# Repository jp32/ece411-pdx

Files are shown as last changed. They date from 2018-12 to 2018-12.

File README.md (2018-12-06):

# Automated Plant Watering Device

This project enables the watering of indoor house plants without being physically present. As various plants need different watering levels, a knob (actually a potentiometer) is set by the user to determine the amount of time to water the plant, which can be set between 5 to 30 seconds. A mositure sensor is used to monitor the soil, in which water is automatically dispensed when the soil is near dry.

## Prerequisites

Boards are pre-installed with the lastest firmware. To upload the test bench firmware the latest version of the Arduino IDE is recommended (free and can be downloaded [here](https://www.arduino.cc/en/Main/Software)).

## Built With
* [Arduino](https://www.arduino.cc/en/Main/Software) - Integrated development environment
* [EAGLE](https://www.autodesk.com/products/eagle/overview) - Schematic and board layout
* [LTspice](https://www.analog.com/en/design-center/design-tools-and-calculators/ltspice-simulator.html) - Circuit simulation
* [GitHub](https://github.com/) - Version control and team collaboration

## Authors

* **Justin Patterson**
* **Jonathan Lampman**
* **Jian Meng**
* **Bruno Duergon**

## License

This project is licensed under the GNU General Public License - see the [LICENSE](LICENSE) file for details

## Acknowledgements
* **Portland State University ECE Department**
* **Andrew Greenberg**
* **Eric Ruhl**

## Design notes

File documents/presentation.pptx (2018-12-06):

## Self watering plant Group 12

Bruno Duregon
Justin Patterson
Jon Lampguy
Jian Meng

## Design matrix

| | Magnetic Gripper | Self Watering Plant | Cleaning Robot | Snack Dispening Machine
Cost | 5 | 1 | 4 | 2 | 4
Feasibility | 5 | 2 | 4 | 2 | 4
Sensor/Actuator Complexity | 2 | 3 | 5 | 2 | 3
Algorithmic Complexity | 3 | 4 | 5 | 1 | 5
Programming Requirements | 5 | 1 | 4 | 1 | 4
Time Commitment | 2 | 2 | 4 | 1 | 2
| Score | 42 | 93 | 34 | 91

## Overview of problem

- Making the home garden watering process more efficient
- Necessity to water house plants without being present
- Rethinking water usage

## Solution

- Self watering plant system
  - Periodically checks moisture level
  - Turns on when moisture level out of bounds
  - Waters appropriate amount

## Block Diagram level 0

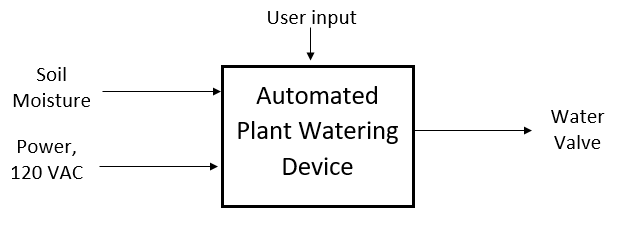
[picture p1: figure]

V DC

## Block diagram level 1

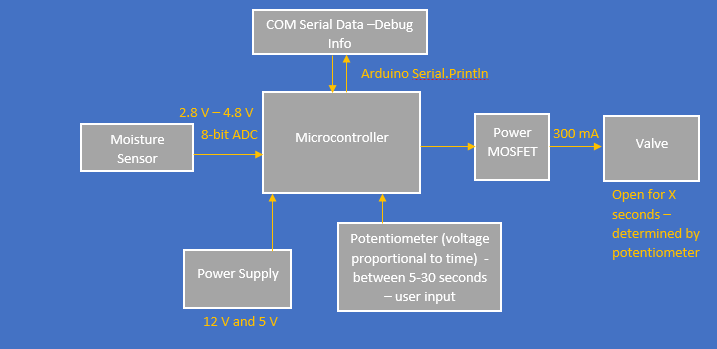
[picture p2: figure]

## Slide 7

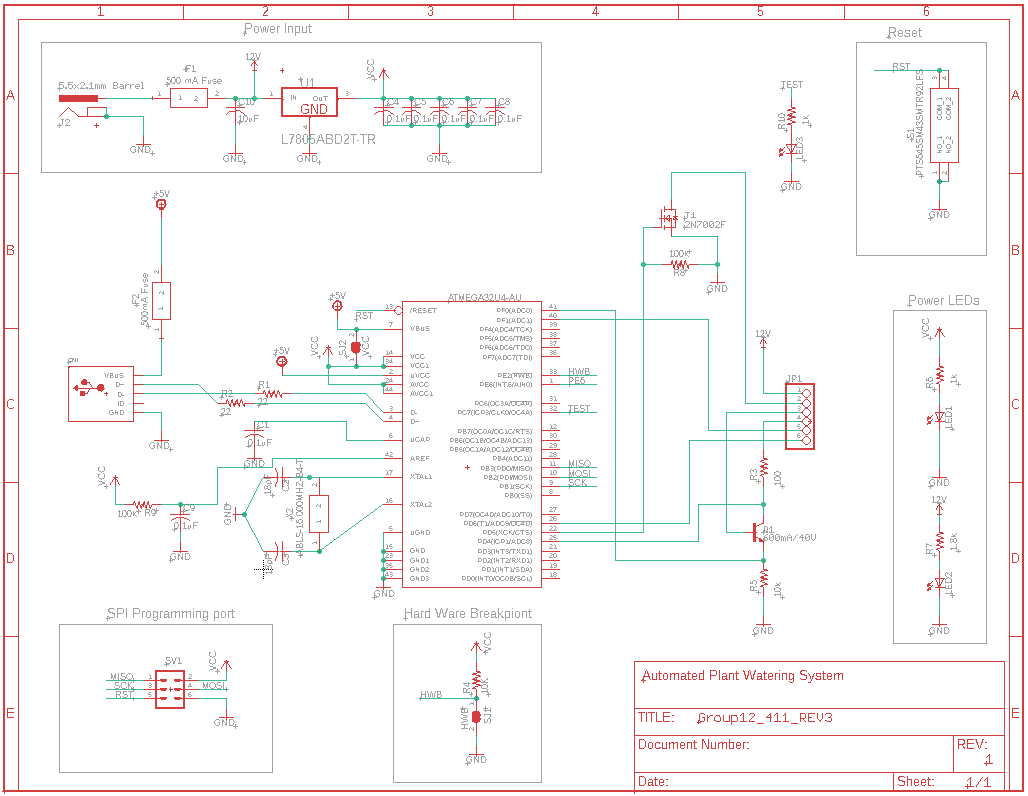
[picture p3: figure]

## layout

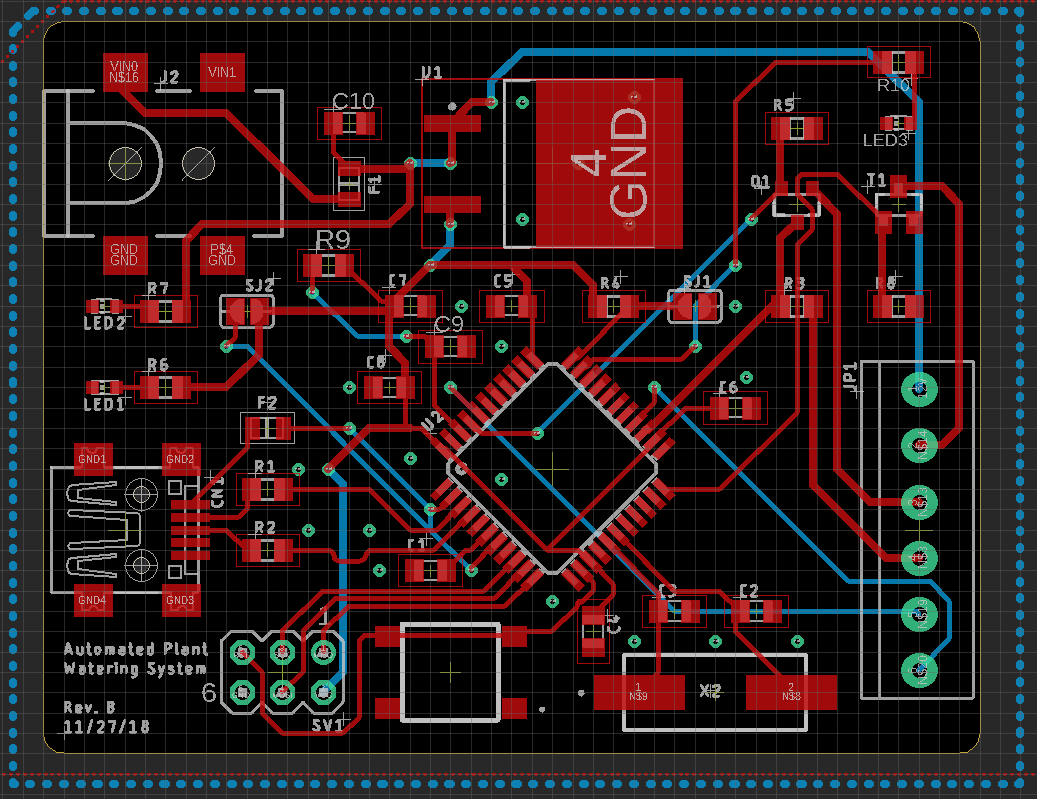
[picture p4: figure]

## Firmware overview

  - If moisture reading is lower than set bounds
    - Water plant for time specified
  - VerificTime specified by potentiometer (between 5 and 30 seconds)
  - ation of hardware via testbench
    - Valve functionalities
      - Open valve, close valve, test potentiometer
    - Sensor functionalities
      - Read sensor once, read sensor x times, read sensor and average

## Bill of Materials

Cnt | Part References | P/DNP | Mfg | Mfg PN | Description | Distributor | Dist. PN | Cost Ea. | Cost Ext.
1 | Microcontroller | P | Microchip Technology | ATMEGA32U4-AUR | AVR AVR® ATmega Microcontroller IC 8-Bit 16MHz 32KB (16K x 16) FLASH 44-TQFP (10x10) | Digikey | ATMEGA32U4-AURTR-ND | 3.49 | 3.49
1 | REG | P | STMicroelectronics | L7805ABD2T-TR | Linear Voltage Regulator IC Positive Fixed 1 Output 5V 1.5A D2PAK | Digikey | 497-1170-1-ND | 0.82 | 0.82
1 | Q1 | P | Diodes Incorporated | DMG3406L-7 | N-Channel 30V 3.6A (Ta) 770mW (Ta) Surface Mount SOT-23 | Digikey | DMG3406L-7DICT-ND | 0.53 | 0.53
2 | R1 | P | TE Connectivity Passive Product | CRGP0805F10K | 10 kOhms ±1% 0.333W, 1/3W Chip Resistor 0805 (2012 Metric) Pulse Withstanding Thick Film | Digikey | A130489TR-ND | 0.02397 | 0.04794
1 | R2 | P | TE Connectivity Passive Product | CRGP0805F100K | 100 kOhms ±1% 0.333W, 1/3W Chip Resistor 0805 (2012 Metric) Pulse Withstanding Thick Film | Digikey | A130501TR-ND | 0.02397 | 0.02397
1 | R3 | P | TE Connectivity Passive Product | CRGP0805F100R | 100 Ohms ±1% 0.333W, 1/3W Chip Resistor 0805 (2012 Metric) Pulse Withstanding Thick Film | Digikey | A130465TR-ND | 0.02397 | 0.02397
1 | R4 | P | TE Connectivity Passive Product | CRGP0805F1K0 | 1 kOhms ±1% 0.333W, 1/3W Chip Resistor 0805 (2012 Metric) Pulse Withstanding Thick Film | Digikey | A130477TR-ND | 0.02397 | 0.02397
1 | R5 | P | Vishay Dale | TNPW08051K80BEEA | 1.8 kOhms ±0.1% 0.2W, 1/5W Chip Resistor 0805 (2012 Metric) Anti-Sulfur, Automotive AEC-Q200, Moisture Resistant Thin Film | Digikey | 541-9859-1-ND | 0.63 | 0.63
2 | R6 | P | TE Connectivity Passive Product | CRGP0805F22R | 22 Ohms ±1% 0.333W, 1/3W Chip Resistor 0805 (2012 Metric) Pulse Withstanding Thick Film | Digikey | A130457TR-ND | 0.02 | 0.04
2 | C1 | P | Samsung Electro-Mechanics | CL21A106KOCLRNC | 10µF ±10% 16V Ceramic Capacitor X5R 0805 (2012 Metric) | Digikey | 1276-2399-2-ND | 0.04428 | 0.08856
6 | C2 | P | Yageo | CC0805ZRY5V9BB104 | 0.1µF -20%, +80% 50V Ceramic Capacitor Y5V (F) 0805 (2012 Metric) | Digikey | 311-1361-1-ND | 0.16 | 0.96
2 | C3 | P | KEMET | C0805C220K5GACTU | 22pF ±10% 50V Ceramic Capacitor C0G, NP0 0805 (2012 Metric) | Digikey | 399-8036-1-ND | 0.14 | 0.28
1 | X1 | P | Abracon LLC | ABLS-16.000MHZ-B4-T | 16MHz ±30ppm Crystal 18pF 40 Ohms HC-49/US | Digikey | 535-10226-1-ND | 0.27 | 0.27
2 | JMP | DNP | Vishay Dale | CRCW08050000Z0EA | 0 Ohms Jumper 0.125W, 1/8W Chip Resistor 0805 (2012 Metric) Automotive AEC-Q200 Thick Film | Digikey | 541-0.0ACT-ND | 0.1 | 0.2
1 | LED(Red) | DNP | Lite-On Inc. | LTST-C191KRKT | Red 631nm LED Indication - Discrete 2V 0603 (1608 Metric) | Digikey | 160-1447-1-ND | 0.29 | 0.29
1 | LED(Green) | DNP | Lite-On Inc. | LTST-C190GKT | Green 569nm LED Indication - Discrete 2.1V 0603 (1608 Metric) | Digikey | 160-1183-6-ND | 0.27 | 0.27
1 | I/O | P | Phoenix Contact | 1985234 | TERM BLOCK PCB 6POS 3.5MM GREEN | Digikey | 277-1626-ND | 0.85 | 0.85
1 | Q2 | P | Micro Commercial Co | MMBT3904-TP | Bipolar (BJT) Transistor NPN 40V 200mA 300MHz 350mW Surface Mount SOT-23 | Digikey | MMBT3904TPMSCT-ND | 0.1 | 0.1
1 | SW1 | P | C&K | PTS645SM43SMTR92 LFS | SWITCH TACTILE SPST-NO 0.05A 12V | Digikey | CKN9112CT-ND | 0.17 | 0.17
2 | FUSE | P | Vishay Beyschlag | MFU0805FF00500P100 | FUSE BOARD MNT 500MA 32VDC 0805 | Digikey | MFU0805.50CT-ND | 0.57 | 1.14
| | | | | | | | | 0
| | | | | | | TOTAL COST: | | $ 10.25

## Test plan 1

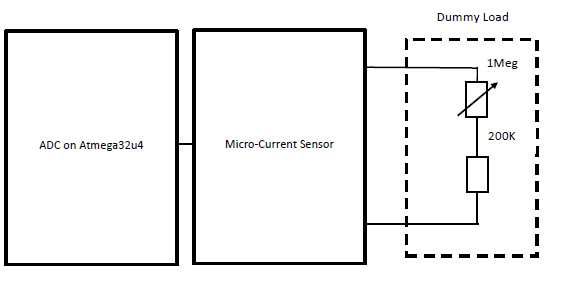
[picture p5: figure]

## Test plan 2

PART 1: Initial Power Setup
1. Before Power is provided to the board for the first time a visual inspection should be
performed by a at least one person whom is not the assembler.
2. Power module test:
a. Power cable connection test
b. Voltage regulator test
3. Power up test:
a. Current level test
b. Voltage level check
c. Leakage check: Check movement of current between two conductors that are not
connected.
d. Opens Test: Check to make sure there is current flow from one "node" to the next
for every net on the board, again by measuring the amount of resistance of the
conductor.
e. Shorts Test: Check to make sure that NO current flows between separate nets by
measuring the amount resistance between them.
2
PART 2: System test
The test session of the system includes two parts:
1. Single component test:
a. Check the type and the specification model of the sensor and actuator
b. Test the functionality of the sensor and actuator
2. System test:
a. Design Validation: PCB Layout validation and code verification.
b. Manufacturing test: Detect the manufacturing defects.
c. Function test: Follow the block diagram of the system to make sure each part of
the system can work correctly.
PART 2 - 1 - 1: Moisture sensor test (FINISHED)
A. Structure of the sensor: Moisture sensor is testing the resistance across two probes, the
moisture level of the soil is represented as the voltage value.
B. Test Method: Plug the probes into the different soil samples(each soil sample got
different level moisture), measure the returned voltage level.
C. Results: By increasing the moisture level of the sample soil, the measured maximum
voltage level is about 4.3V(Under 5V power supply voltage). The minimum voltage level
is about 2V.
PART 2 - 1 -

PART 2 - 1 - 2: Actuator Test (FINISHED)
The actuator of the automated watering system is a water valve. The I/O pin of the processor
control the ON and OFF of the actuator. When the moisture level lower than the threshold value,
3
the system will turn on the valve. In other words, the goal of the test is to make sure that the
actuator is capable for multiple ON/OFF in a short time period.
A. Test Method: Connect the valve to the output pin of the circuit, run the “Blink” file on
the circuit.
B. Results: Run the program for 2 minutes, the system will keep turning ON/OFF of the
valve, the valve worked correctly.
PART 2 - 2 - 1: PCB Validation
A. Parts completion check:
a. All major components included?
i. Processor
ii. Power supply (Voltage regulator)
iii. Moisture sensor
iv. The actuator (Valve)
b. All support components included?
i. USB connection port
ii. Power connection port
iii. Reset switch
c. All the surface mount circuit component included?
B. PCB footprint check
C. Parts placement test
PART 2 - 2 - 2: Function Test
A. Debug the code to make sure the code can successfully flash into the processor.
4
B. After the program is flashed to the processor via USB, a test run should be performed.
PART 2 - 2 - 3: Manufacturing Test
A. Follow the schematic and assemble the circuit on each board.
B. Follow the test method in PART 2 - 2 - 2 to test all the prototypes.

## what’s left to do

- Second revision of board (fix board issue)
- Put it in box – waterproof it
- More I/O for sensors and plants
- Keep historical data for seasonal average
- Add wireless communication for viewable diagnostics and statistics (phone, computer, app)

## Finalized gantt chart

## Lessons learned

- Board layout took longer than expected
- Be careful with discount power supplies
- No lull time – always stay on top of something
- Be careful soldering, we only have four boards
- Can have greater spacing between traces (it’s okay)

Jon lowkey farts a lot in the lab

## IP used

- Eagle
- LT Spice
- Microsoft Office
- GitHub (https://github.com/jp32/ece411-pdx)
- Arduino

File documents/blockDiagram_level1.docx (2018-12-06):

# Automated Plant Watering Device: Level 1

Potentiometer (voltage proportional to time) - between 5-30 seconds – user input

12 V and 5 V

Power Supply

2.8 V – 4.8 V

Arduino Serial.Println

COM Serial Data –Debug Info

300 mA

8-bit ADC

Moisture Sensor

Open for X seconds – determined by potentiometer

Valve

Power MOSFET

Microcontroller

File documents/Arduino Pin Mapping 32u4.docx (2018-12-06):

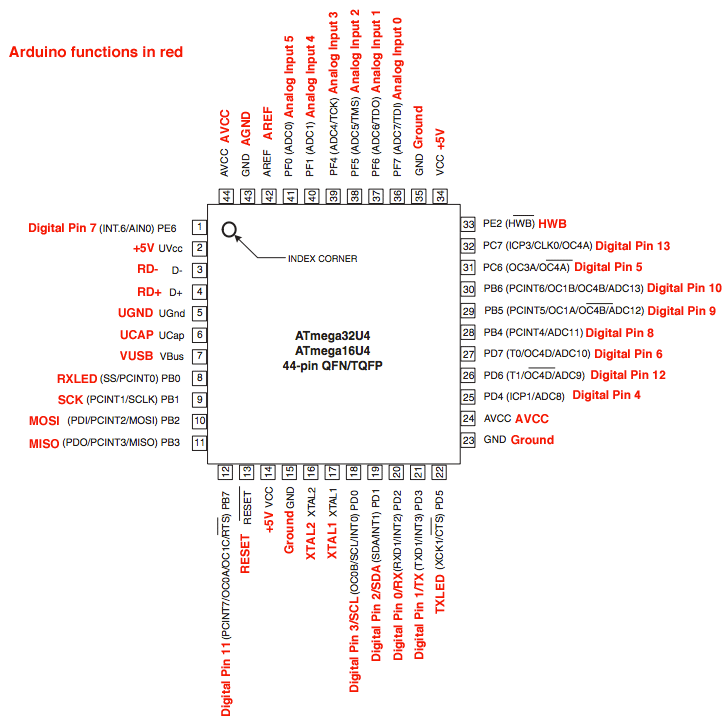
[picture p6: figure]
Image result for 32u4 arduino

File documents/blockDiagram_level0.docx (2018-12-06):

# Automated Plant Watering Device: Level 0

User input

Soil

Moisture

Automated Plant Watering Device

Water

Valve

Power,

120 VAC

Module | Automated Plant Watering Device
Inputs | Soil moisture: ?-?V Power: 120V AC rms, 60 Hz
Outputs | Water valve: voltage controlled, 12V
Functionality | Provide water to plant. The length of time the valve is open is inversely proportional to the soil moisture. i.e., Lower moisture → more water

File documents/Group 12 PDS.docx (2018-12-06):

Product Design Specification

Group 12

Justin Patterson, Jian Meng, Jonathan Lampman, Bruno Duregon

Executive Summary/Concept of Operations:

The intention of our project is to create a device that can monitor the moisture level in soil, to then appropriately open a valve to water a plant. For our project, the valve is an emulation of the device being hooked up to some real water source. It is targeted towards the average consumer, but can be used in many different applications: can be useful for plants that need to be watered rarely (potentially store historic data and water accordingly), used in any application where self-watering is required (can change watering amount decision criteria as needed), or is useful in accurately watering a plant the required amount (no overwatering, potential area to conserve resources in).

Brief Market Analysis:

The intended customers of our product are homeowners, renters, anybody with some sort of small to medium sized plant, potted or in the soil. Our product is looking to be sold around the $20 mark, as it can only serve one plant. In the future, a potential update to our product model would be to sell extension tubes so one unit could water multiple plants at a time.

Requirements:

- Must measure relative moisture content
- Must distribute water depending on relative moisture content
- Should retain semi-historic data and take it into account when decision making
- Must run on 9V battery
- Should interface to LCD screen for easily viewable information
- Should be portable

System Architecture:

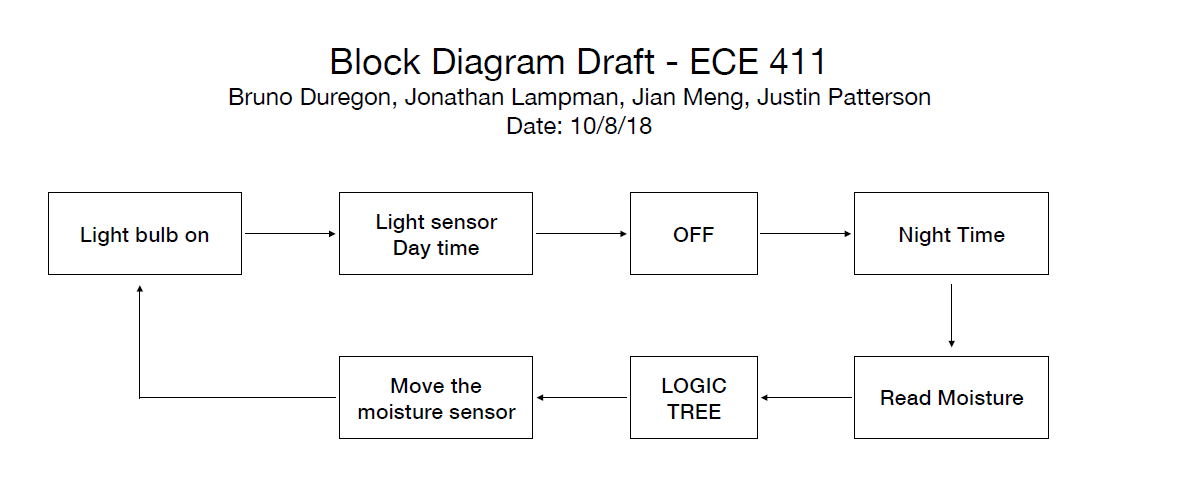
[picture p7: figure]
A screenshot of a cell phone Description generated with very high confidence

Design Specification:

- Sensor: TBD
- Actuator: Plastic Water Solenoid Valve - 12V - 1/2 Nominal, 3-116 PSI (0.21 ~ 8 bar), Connection Method: Threaded ½” NPS, 0.01 lb (4.54g)
- ATMEGA32U4 AVR 8-Bit Microcontroller, Max Clock Frequency: 16 MHz, Program Memory Size: 32 kB, Data RAM Size: 2.5 kB, ADC Resolution: 10 bit, Number of I/Os: 26 I/O, Operating Supply Voltage: 2.7 V to 5.5 V
- Arduino programmer

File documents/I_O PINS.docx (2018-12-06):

Water Valve Output: Digital Pin 1

Output High to turn on valve

Moisture Sensor Input: Analog Input 5

Most wet will be high of around 4.3 Volts

Photo Resistor out: Digital Pin 12

Photo Resistor In: Analog Input 4

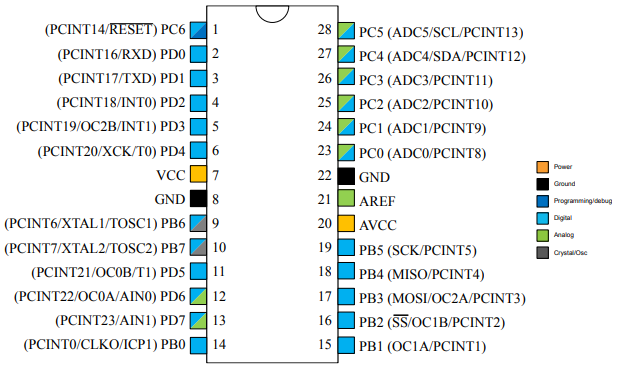
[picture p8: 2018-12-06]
datasheets/ATmega328-328P_pinout.png

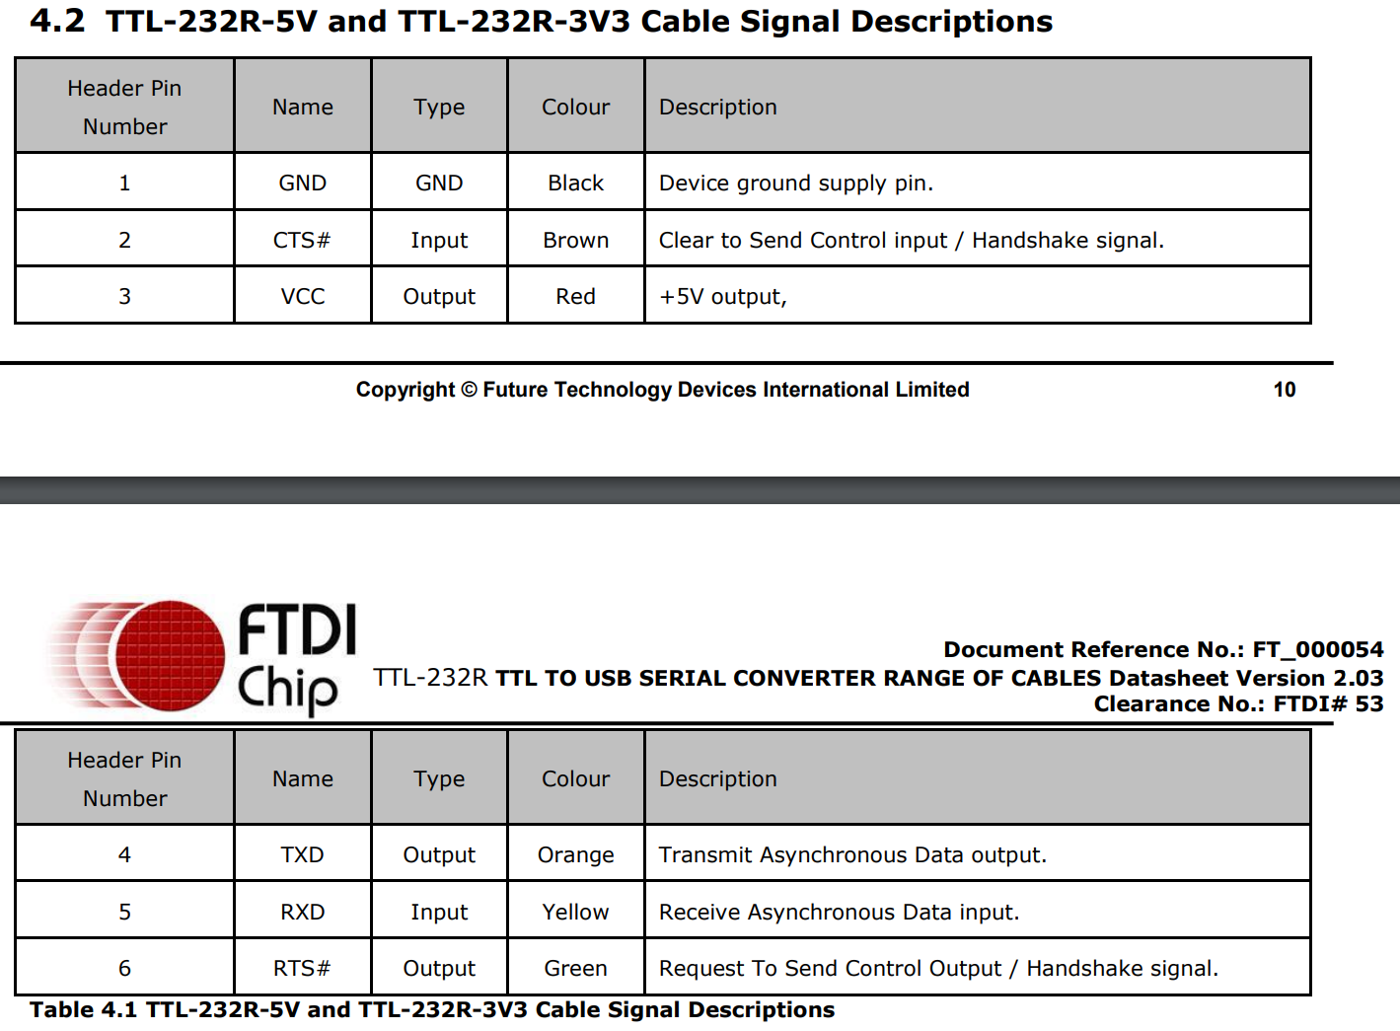
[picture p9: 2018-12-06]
datasheets/TTL-232R-5V_Cable_Signal.PNG

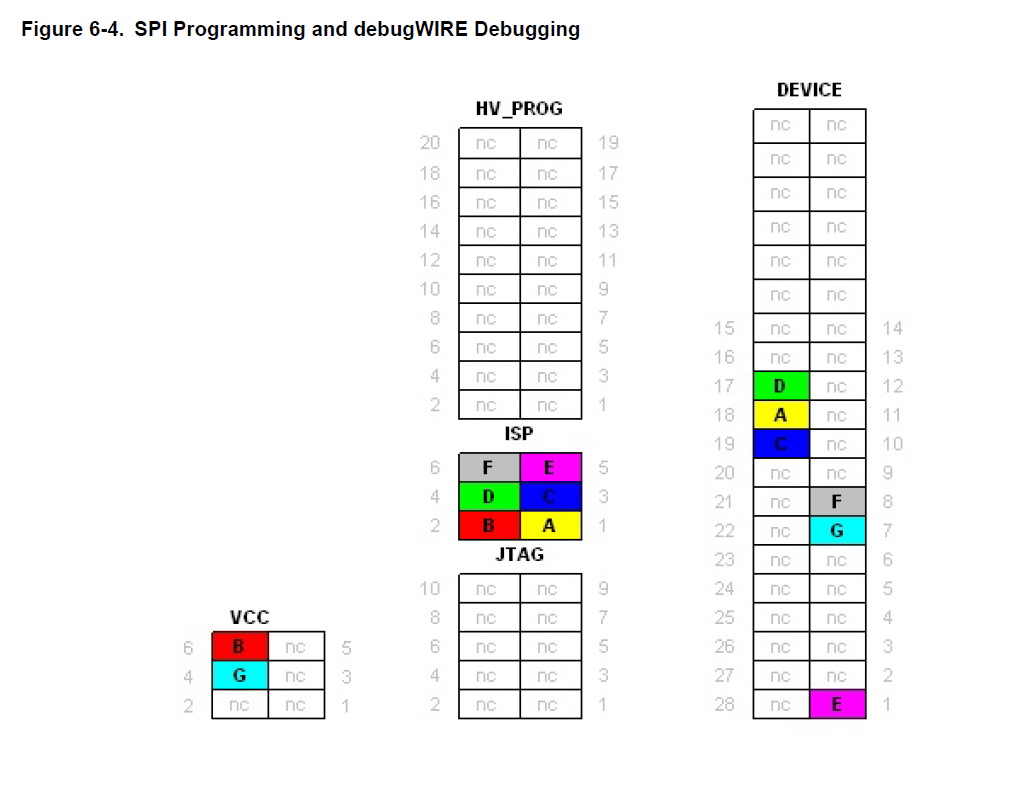
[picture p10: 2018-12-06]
datasheets/SPI_Prog.png

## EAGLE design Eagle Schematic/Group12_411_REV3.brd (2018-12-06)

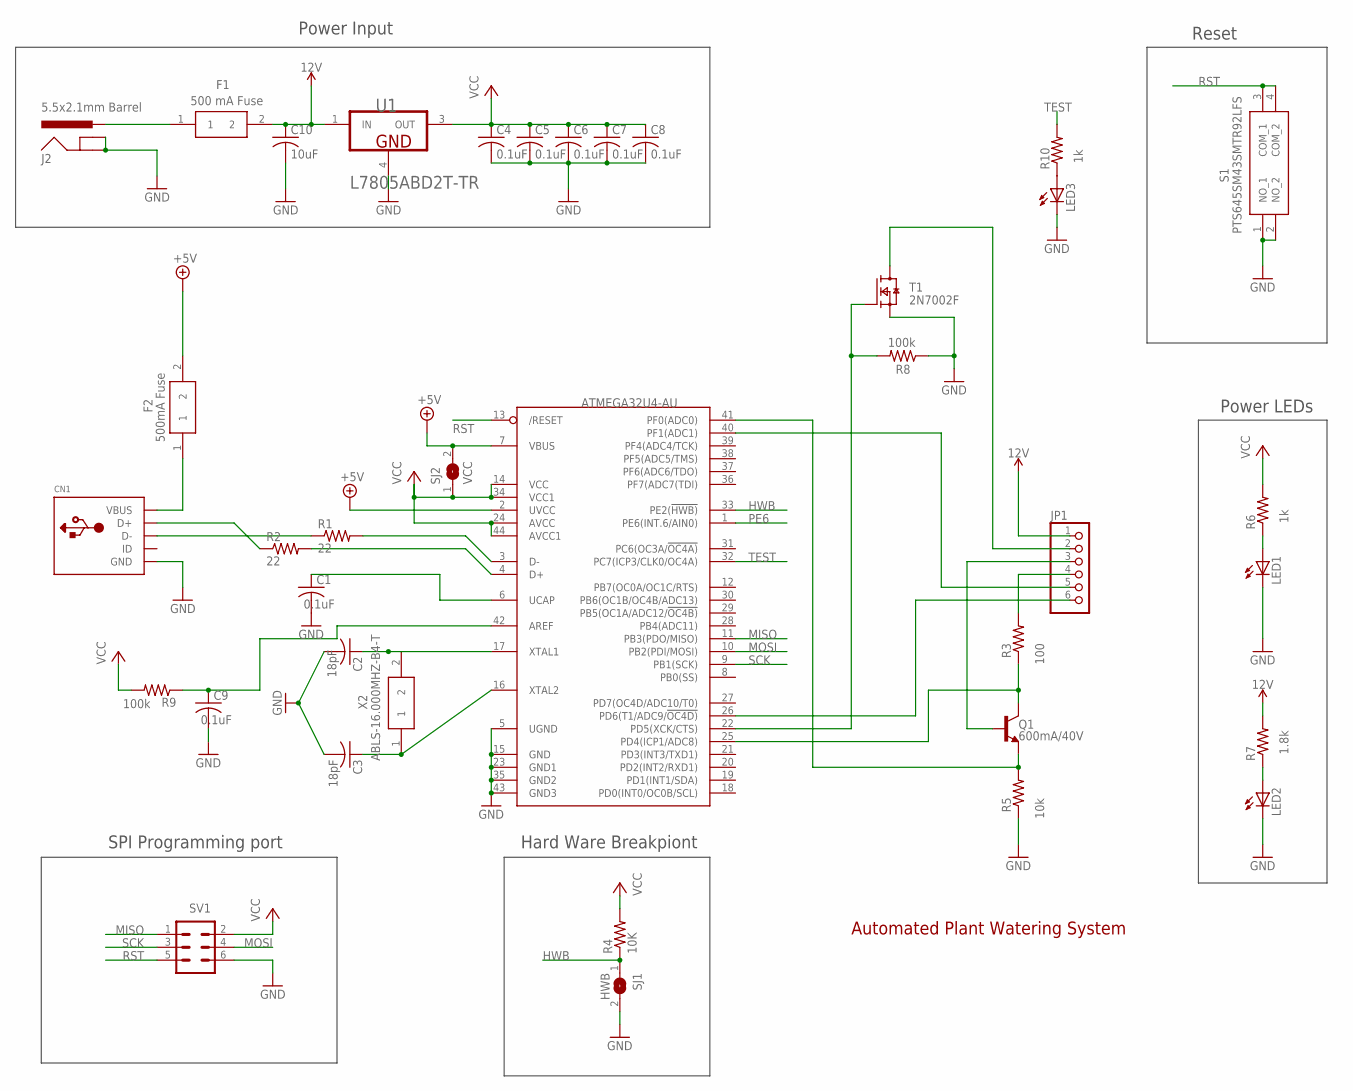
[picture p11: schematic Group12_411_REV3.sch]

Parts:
C1, C4, C5, C6, C7, C8, C9: 0.1uF; C0805K
C2, C3: 18pF; C0805K
C10: 10uF; C0805K
CN1: USBMINIB; USB-MINIB
F1: MFU0805FF00500P100; FUSC2012X55N; MANUFACTURER_PART_NUMBER 500 mA Fuse
F2: MFU0805FF00500P100; FUSC2012X55N; MANUFACTURER_PART_NUMBER 500mA Fuse
J2: 5.5x2.1mm Barrel; POWER_JACK_SMD
JP1: PINHD-1X6-3.5MM; 1X06-3.5MM
LED1, LED2, LED3: LEDCHIP-LED0603; CHIP-LED0603
Q1: 600mA/40V; SOT23-3
R1, R2, R3, R5: 22; R0805
R4, R6, R7, R8, R10: 10K; R0805
R9: 100k; R0805
S1: PTS645SM43SMTR92LFS; PTS645SMT
SJ1: HWB; SJ
SJ2: VCC; SJ
SV1: MA03-2
T1: 2N7002F; SOT23
U1: STMICROELECTRONICS_L7805ABD2T-TRSTMICROELECTRONIC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; STMICROELECTRONICS_L7805ABD2T-TR_0
U2: ATMEGA32U4-AU; TQFP44
X2: ABLS-16.000MHZ-B4-T; ABLS

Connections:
12V: C10.1, F1.2, JP1.1, R7.2, U1.1 (IN)
+5V: F2.2, SJ2.2, U2.2 (UVCC), U2.7 (VBUS)
GND: C1.2, C2.2, C3.2, C4.2, C5.2, C6.2, C7.2, C8.2, C9.2, C10.2, CN1.GND, J2.GND (GNDBREAK), J2.P$4 (GND), LED1.C, LED2.C, LED3.C, R5.1, R8.1, S1.1 (NO_1), S1.2 (NO_2), SJ1.2, SV1.6, T1.2 (S), U1.4 (GND), U2.5 (UGND), U2.15 (GND), U2.23 (GND1), U2.35 (GND2), U2.43 (GND3)
HWB: R4.1, SJ1.1, U2.33 (PE2(!HWB))
MISO: SV1.1, U2.11 (PB3(PDO/MISO))
MOSI: SV1.4, U2.10 (PB2(PDI/MOSI))
unnamed: LED3.A, R10.1
unnamed: CN1.D+, R2.1
unnamed: JP1.4, R3.2
unnamed: R2.2, U2.4 (D+)
unnamed: CN1.D-, R1.1
unnamed: C1.1, U2.6 (UCAP)
unnamed: R1.2, U2.3 (D-)
unnamed: C2.1, U2.17 (XTAL1), X2.2
unnamed: C3.1, U2.16 (XTAL2), X2.1
unnamed: LED1.A, R6.1
unnamed: Q1.3 (C), R3.1, U2.25 (PD4(ICP1/ADC8))
unnamed: Q1.2 (E), R5.2, U2.41 (PF0(ADC0))
unnamed: JP1.3, Q1.1 (B)
unnamed: JP1.2, T1.3 (D)
unnamed: LED2.A, R7.1
unnamed: F1.1, J2.VIN0 (PWR)
unnamed: CN1.VBUS, F2.1
unnamed: R8.2, T1.1 (G), U2.22 (PD5(XCK/CTS))
unnamed: JP1.5, U2.40 (PF1(ADC1))
unnamed: JP1.6, U2.26 (PD6(T1/ADC9/!OC4D))
unnamed: C9.1, R9.1, U2.42 (AREF)
PE6: U2.1 (PE6(INT.6/AIN0))
RST: S1.3 (COM_1), S1.4 (COM_2), SV1.5, U2.13 (/RESET)
SCK: SV1.3, U2.9 (PB1(SCK))
TEST: R10.2, U2.32 (PC7(ICP3/CLK0/OC4A))
VCC: C4.1, C5.1, C6.1, C7.1, C8.1, R4.2, R6.2, R9.2, SJ2.1, SV1.2, U1.3 (OUT), U2.14 (VCC), U2.24 (AVCC), U2.34 (VCC1), U2.44 (AVCC1)

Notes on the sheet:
Automated Plant Watering System
Power Input
Reset
Power LEDs
SPI Programming port
Hard Ware Breakpiont

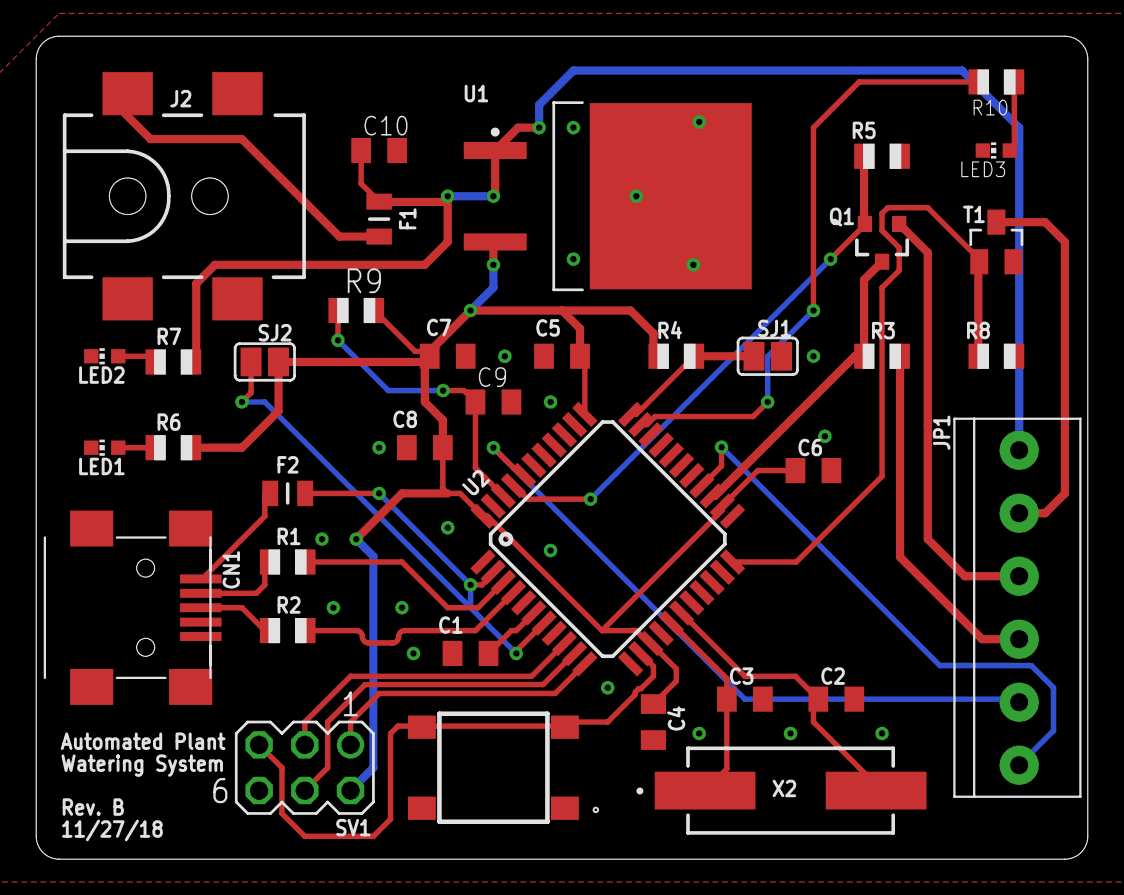
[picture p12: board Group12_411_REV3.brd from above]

Board: 2 copper layers, 58.4 x 45.7 mm, 37 parts (0 on the bottom side), 31 nets.

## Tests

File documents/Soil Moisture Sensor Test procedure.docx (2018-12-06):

Soil Moisture Sensor Test procedure

Dummy Load

ADC on Atmega32u4

Micro-Current Sensor

1Meg

200K

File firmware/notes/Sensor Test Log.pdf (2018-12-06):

Friday, November 30, 2018

## Sensor Test

Moisture sensor test

- Lower bound: 3.6V - 658 digital value - 1Mega ohms
- Upper bound: 4.7V - 896 digital value - 120 ohms
- Middle value: 4.0 V - 764 digital value - 0.436 Mega ohms

1

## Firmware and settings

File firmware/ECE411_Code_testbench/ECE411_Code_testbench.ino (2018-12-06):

/* ECE 411 Practicum Project - Jian Meng
   =========================
   Automatic Watering system
   =========================
   November 18 2018
*/

// Initialize the variables
int soilpin = A5; // Declare a pin for the soil moisture sensor
int UserSet = A4; // Declare a pin for the user to set water amount
int Soilpower = 4; // Declare the power pin of the sensor
int UserPower = 12; //Declare the power ping for user setting
int Valvepower = 1;
int count = 0;
int M_UpperBound = 857;  // Upper bound of the moisture level
int M_LowerBound = 750;  // Lower bound of the moisture level
int sensorValue;         // The variable of the moisture value
int UserValue;           // The variable of the user setting value
String greetString = "Enter Mode of Operation: \nrun - start normal operating procedure \ntest - enter test bench mode";

char* sensorTestOptions[] = {
  "1. Read sensor once",
  "2. Read sensor x times",
  "3. Read sensor x times and collect average"
};

void setup() {
  // Initial Setup
  Serial.begin(9600); // Serial port
  pinMode(Soilpower, OUTPUT);  // Set the power pin of the sensor as the output
  pinMode(Valvepower, OUTPUT); // Set the power pin of the valve as the output
  digitalWrite(Valvepower, LOW); // Set to LOW so no power is flowing through the valve
  digitalWrite(Soilpower, LOW); // Set to LOW so no power is flowing through the sensor

  while (!Serial);
  Serial.println(greetString);
}

// Moisture Reading Function
int readMoisture()
{
  digitalWrite(Soilpower, HIGH);  // Turn on the transistor
  delay(10); // Wait 10 milliseconds
  int val = analogRead(soilpin);  // Read the moisture value
  Serial.print("Moisture value = ");
  Serial.println(val);   // Print the value back to the serial port
  digitalWrite(Soilpower, LOW); // Turn off the transistor
  return val;  // Return the moisture value
}

int readUserSetting()
{
  digitalWrite(UserPower, HIGH);  // Turn on voltage divider
  delay(10); // Wait 10 milliseconds
  int val2 = ((pow(analogRead(UserSet), 3) / 13000) - 1000); // Read the user valve open time setting non-linear
  Serial.print("Valve open value = ");
  Serial.println(val2);   // Print the value back to the serial port
  digitalWrite(UserPower, LOW); // Turn off voltage divider
  return val2;  // Return the moisture value
}

// Valve control function
int valveControl()
{
  digitalWrite(Valvepower, HIGH);
  Serial.println("Valve is on, delaying...");
  delay(UserValue);
}

void loop() {
  if (Serial.available()) {
    String cmd = Serial.readString();

    if (cmd == "run\n") {
      // The loop will keep check the moisture level of the soil
      Serial.print("Wait for two seconds");
      delay(2000);
      // serial print "done waiting two seconsd - reading moisture"
      sensorValue = readMoisture(); // Read the moisture level
      UserValue   = readUserSetting(); //Read the user setting
      if (sensorValue <= M_LowerBound && (sensorValue > 100)) {
        Serial.print("Current moisture value = ");
        Serial.println(sensorValue);
        Serial.print("Current user value = ");
        Serial.println(UserValue);
        // If the moisture value lower than the lower bound, turn on the valve for 30 seconds
        valveControl();
        digitalWrite(Valvepower, LOW); // Turn off the valve.
      }
    }
    else if (cmd == "test\n") {
      Serial.println("* ENTERED DEBUG MODE *");
      Serial.println("* Choose debug function");
      Serial.println("* Press 1 for valve functions \n* Press 2 for sensor functions");
      Serial.println("* Waiting for user input...");
      while (Serial.available() == 0) {}
      String testcmd = Serial.readString();

      if (testcmd == "1\n") {
        Serial.println("** ENTERED VALVE MODE *");
        Serial.println("** Choose debug function");
        Serial.println("** Press 1 to open valve \n** Press 2 to close valve \n** Press 3 to open valve for 5-30 seconds (potentiometer)");
        while (Serial.available() == 0) {}
        String valvecmd = Serial.readString();

        if (valvecmd == "1\n") {
          Serial.println("*** Opening valve");
          digitalWrite(Valvepower, HIGH);
          Serial.println(greetString);
          return 0;
        }
        else if (valvecmd == "2\n") {
          Serial.println("*** Closing valve");
          digitalWrite(Valvepower, LOW);
          Serial.println(greetString);
          return 0;
        }
        else if (valvecmd == "3\n") {
          Serial.println("*** Opening valve for 5-30 seconds...");
          UserValue   = readUserSetting(); //Read the user setting
          Serial.print("*** Delaying valve for ");
          Serial.print(UserValue / 1000);
          Serial.println(" seconds");
          digitalWrite(Valvepower, HIGH);
          delay(UserValue);
          digitalWrite(Valvepower, LOW);
          Serial.println(greetString);
          return 0;
        }

      }
      else if (testcmd == "2\n") {
        Serial.println("** ENTERED VALVE MODE *");

        sensor_test:
        PrintSensorTestOptions();

        while (Serial.available() == 0) {}
        String sensorCmd = Serial.readString();
        if (sensorCmd == "1\n")
        {
          Serial.println("Reading sensor once...");
          readMoisture();
          
          Serial.println(greetString);
          
          return 0;
        }
        else if (sensorCmd == "2\n")
        {
          Serial.println("Enter number of times to read sensor.");
          
          while (Serial.available() == 0) {}
          int sensorReadNum = Serial.parseInt();
          
          Serial.print("Reading sensor ");
          Serial.print(sensorReadNum);
          Serial.println(" times...");
          
          for (int i = 0; i < sensorReadNum; i++)
          {
            readMoisture();
          }
          
          Serial.println(greetString);
          
          return 0;
        }
        else if (sensorCmd == "3\n")
        {
          Serial.println("Enter number of times to read sensor.");
          
          while (Serial.available() == 0) {}
          int sensorReadNum = Serial.parseInt();
          
          Serial.print("Reading sensor ");
          Serial.print(sensorReadNum);
          Serial.println(" times and collecting average...");

          long sum = 0;
          int moist = 0;
          for (int i = 0; i < sensorReadNum; i++)
          {
           
            moist = readMoisture();
            sum = sum + moist;
            Serial.println(sum);
          }

          Serial.print("Average moisture = ");
          Serial.println(sum/sensorReadNum);
          Serial.print("Sum = ");
          Serial.println(sum);
          Serial.print("sensorReadNum = ");
          Serial.println(sensorReadNum);
          
          Serial.println(greetString);
          
          return 0;
        }
        else
        {
          Serial.println("Invalid number!");
          goto sensor_test;
        }
      }
    }
    else {
      return;
    }

  }
  else {

  }
}

void PrintSensorTestOptions()
{
  for (int i = 0; i < sizeof(sensorTestOptions) / sizeof(sensorTestOptions[0]); i++)
  {
    Serial.println(sensorTestOptions[i]);
  }
}

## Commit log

2018-10-23 Create Eagle Schematic
    All Times Eagle CAD
2018-10-23 Create Eagle Schematic
    All Things Eagle
2018-10-23 Create Eagle Schematic
2018-10-23 Create Eagle Schematic
    looooo
2018-10-23 Create Eagle Schematic
    sdf
2018-10-24 Still needs work on the Programming Dongle
    [411_REV0.sch]
2018-10-24 Schematic Still needs work on the Programming Dongle
    [411_REV0.sch]
2018-10-25 Eagle Schematic turned In on 10/25
    [411_REV0.sch, Group12_411_REV0.sch]
2018-10-29 Code for Arduino Bootloader
    Credit to Nick Gammon. Instructions at https://www.gammon.com.au/bootloader
2018-11-09 Added Switch
    [BOM.xlsx]
2018-11-09 Add L78 voltage regulator datasheet
2018-11-11 Updated BOM and New Eagle Schematic
    [BOM.xlsx, Group12_411_REV2.sch]
2018-11-12 Added d2pak for linear reg
    [BOM.xlsx]
2018-11-12 Changed Q1 to SMD
    [BOM.xlsx]
2018-11-12 Update switch in BOM
    [BOM.xlsx]
2018-11-12 LED updated
    [BOM.xlsx]
2018-11-12 Changed power transistor
    [BOM.xlsx]
2018-11-12 Add fuse to BOM
    [BOM.xlsx]
2018-11-12 Added r
    [BOM.xlsx]
2018-11-12 General updates
    [BOM.xlsx]
2018-11-13 For realllllzz
    [Group12_411_REV2.sch]
2018-11-13 eagle shiz
    [Group12_411_REV2.brd, Group12_411_REV2.sch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]
2018-11-15 Cross your fingers
    [Group12_411_REV3.brd, Group12_411_REV3.sch]
2018-11-15 BOM for digikey
    [BOM that you can use in digi-key.xlsx]
2018-11-26 Decision Matrix Added
    [matrix.xlsx]
2018-11-28 Update Eagle Schematic and Board
    Connect +5V on board, and add a programmable LED on pin 32 for testing
    [Group12_411_REV3.brd]
2018-11-28 Useful Documents
    [BOM that you can use in digi-key.xlsx]
2018-12-01 Arduino_Code V0.9
2018-12-05 Changed valve stuff (test)
2018-12-05 Added presentation and sensorvalue > 100
2018-12-06 Add sensor test for testbench
2018-12-06 Dev branch file clean-up
    [Group12_411_REV0.sch, Group12_411_REV1.sch, Group12_411_REV2.brd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]

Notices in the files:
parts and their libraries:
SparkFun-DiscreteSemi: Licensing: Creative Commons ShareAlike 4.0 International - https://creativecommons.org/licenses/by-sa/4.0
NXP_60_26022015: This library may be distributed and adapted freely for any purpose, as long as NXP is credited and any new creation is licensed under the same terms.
